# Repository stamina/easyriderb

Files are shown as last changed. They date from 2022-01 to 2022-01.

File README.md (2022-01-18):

EasyRider
=========

This project is frozen. It's here for archival/educational purposes.

_UPDATE:_ EasyRider REV C is a completely new project, it is based on
a way more powerful (32bit instead of 8bit) STM32 Arm Cortex M4 microcontroller.

EasyRider REV B is a motorcycle telemetrics project, developed specifically for my Honda C90 classic bike.
It uses more advanced code and SMD components than Rev A.

The software is written in bare-metal C for the Atmel AVR ATmega1284p 8bit microcontroller.

The PCB was created with Altium, you'll find the gerbers/schematics/datasheets in the /docs directory.

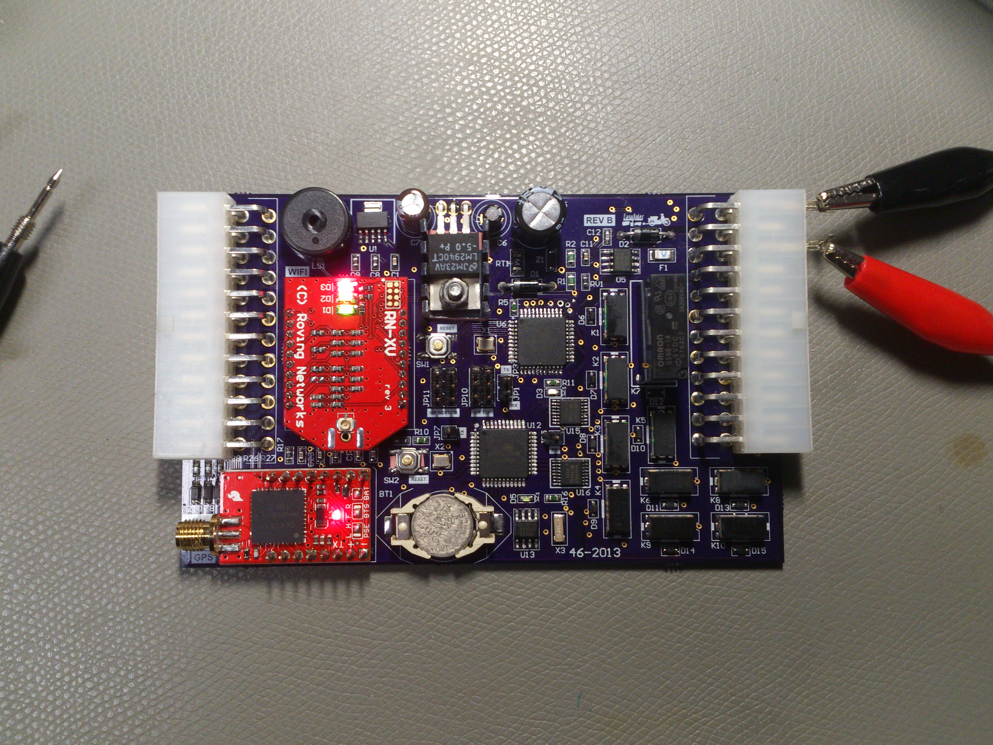
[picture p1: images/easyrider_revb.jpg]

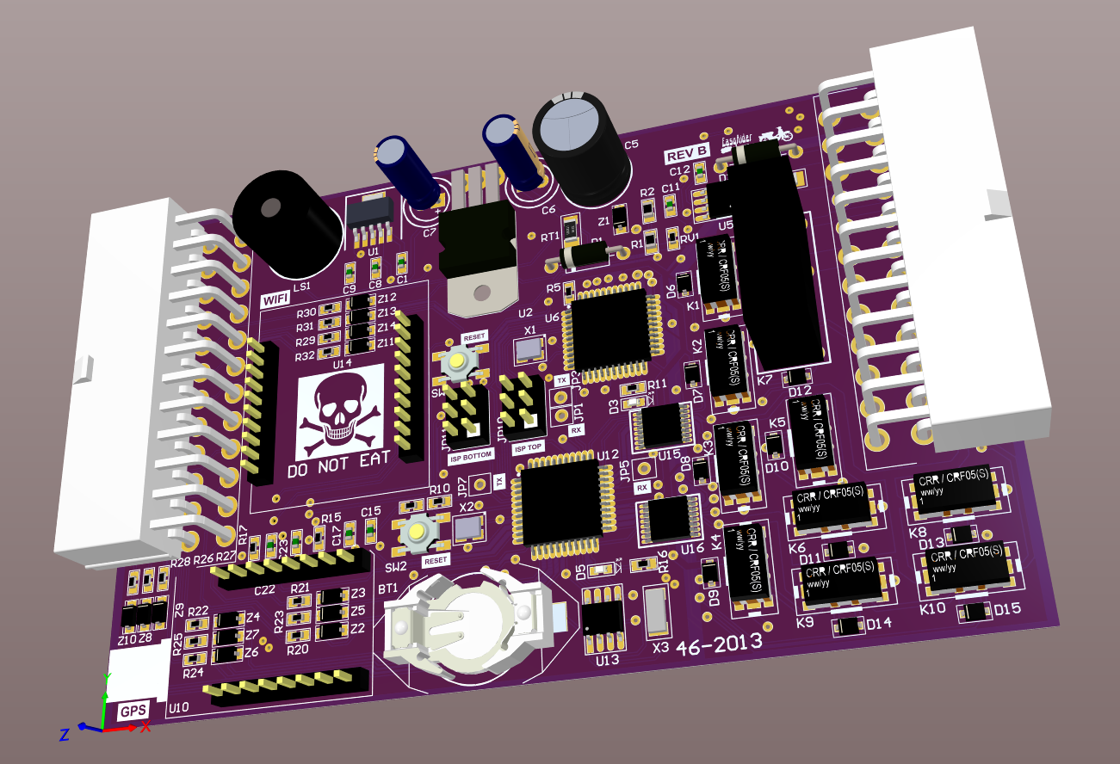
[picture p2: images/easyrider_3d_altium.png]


Functionality
-------------

EasyRider basically does the following things:

- Controls the lighting system: indicators, rear light, brake light, etc.
- Controls the claxon
- Contains a simple alarm system, based on an accelerometer
- Reads the motorcycle battery voltage and the power draw of the board
- Contains a little buzzer for some startup/alarm sounds
- Reads the RPM of the motor via the CDI, through an opamp and optocoupled circuit
- Logs GPS coordinates and timestamps of events via the external RTC
- Sends all telemetry data over Wifi or writes it to the microSD card

Notable components
------------------
2x Atmel AVR ATmega1284P microcontrollers
1x Accelerometer MMA7361L board
1x GPS Venus638FLPx sparkfun board
1x WiFly-RN-XV-DS sparkfun board
1x lm35 temperature sensor
9x Meder reed relays CRR05-1A
1x Opamp tlv2371
1x Optocoupler vo610a
1x Real Time Clock DS1307.pdf
2x uln2003lv transistor arrays

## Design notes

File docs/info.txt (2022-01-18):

*info.txt* easyrider rev B
" vim: filetype=help foldmethod=marker foldmarker=<<<,>>> modifiable noreadonly tw=0
" Author: Bas Brugman
" Website: www.visionnaire.nl

EasyRider REV B
---------------

General functionality
---------------------

Steps for firmware setup new boards:

  1. Set correct fuses via avr.txt
  2. remove HALT bit from RTC register: run ds1307_start_osc() once from init
  3. setup GPS (default baudrate is 9600 -> setting to 56700):
     3 uart strings with baud rate, 10hz and binary msg only
     -> Paste them from setup.h into mcu2 .c file
  4. setup WIFI via UART commands:
     Default baudrate is 9600, change this after initial setup to 57600
     Firmware update to 4.41, see below
     -> Serial setup of Wifly is done by the cutecom or moserial terminal program.
     -> Paste the pass-through UART code from setup.h into mcu1 .c file

Communication
-------------

[X] SPI bus (for MCU intercommunication and microSD card reading/writing):

  System Commands API (SPI Intercommunication between mcu's to exchange data)

  SPI Intercommunication conditions and command logic:

  SPI speed: fosc/4 (20 Mhz) -> 5 Mhz

  MCU intercommunication time per byte is: 32 (8 bits*4 prescaler) cycles + 2 gap cycles + 5us delay added per byte ->

  6.7us per byte -> 145 Kbyte/sec throughput

  Per second througput needed:

  mcu1 IN buffer:
    10x ~96 bytes GPS
    10x ~44 bytes DATA
        ~49 bytes other triggered cmds

  mcu2 IN buffer:
    10x ~29 bytes STATS
       ~119 bytes other triggered cmds

  Feedback / Flow Control / Queueing system:

  OnChange triggered commands have higher priority than Timed command triggers, so they stop/flush the current out cmds buffers and take
  over the communication buffers.

  SPI Flow between both mcu's and WiFi module:

app     <--------[ wifi or serial (uart0/1 from mcu1 ]---------->    mcu1      <----------[ SPI ]------------->    mcu2
=======================================================================================================================
                                                                            state change trigger <---  CMD_STATE  ('a')
                                <--- mcu1 response <--- CMD_STATE ('a')
  ---------------------------------------------------------------------------------------------------------------------
                                                                        periodic trigger <---  CMD_STATS ('b') (10 t/s)
                                                          mcu 1 response ---> CMD_STATS ('b')
  ---------------------------------------------------------------------------------------------------------------------
                                                                         periodic trigger <---  CMD_DATA ('c') (10 t/s)
                                <--- mcu1 response  <--- CMD_DATA ('c')
  ---------------------------------------------------------------------------------------------------------------------
                                                                          periodic trigger <---  CMD_GPS ('d') (10 t/s)
                                 <--- mcu1 response  <--- CMD_GPS ('d')
  ---------------------------------------------------------------------------------------------------------------------
                  --->   on app trigger ---> CMD_RTC ('e')
                                                           CMD_RTC ('e') ---> on response ---> 
  ---------------------------------------------------------------------------------------------------------------------
                  --->   on app trigger ---> CMD_SENSE ('f')
                                                           CMD_SENSE ('f') --> on response ---> 
  ---------------------------------------------------------------------------------------------------------------------
                  --->   on app trigger ---> CMD_SETTINGS ('g')
                                                           CMD_SETTINGS ('g') --> on response ---> 
  ---------------------------------------------------------------------------------------------------------------------
                  --->   on app trigger ---> CMD_LOG ('h')
                                                           CMD_LOG ('h') --> on response ---> 
                                                                                     <----- on response  CMD_LOG ('h')
  ---------------------------------------------------------------------------------------------------------------------
                  --->   on app trigger ---> CMD_REBOOT ('i')
                                                           CMD_REBOOT ('i') --> on response ---> 
  ---------------------------------------------------------------------------------------------------------------------
                  --->   on app trigger ---> CMD_PINCODE ('j')
                                                           CMD_PINCODE ('j') --> on response ---> 
  ---------------------------------------------------------------------------------------------------------------------
                                                                                         trigger <---  CMD_SOUND ('k')
                  --->   on app trigger ---> CMD_SOUND ('k')
                                                          mcu 1 handler ('k')
  ---------------------------------------------------------------------------------------------------------------------
                                                                                            trigger <---  CMD_MSG ('l')
                                                           response ('l')
  ---------------------------------------------------------------------------------------------------------------------

  [X] MCU2 is master, MCU1 is slave
    [X] FIX: SS on mcu2 is a input GPIO: SI_LI (left indicator psense) -> ignore EV_LI_ON/EV_LI_OFF during each SPI transfer,
        since SS must be temporarily set as an output(low), then output(high) to not interfere with the hardware SPI
  [X] SPI communication queuing algorithm
      SPI tips: -> http://rpc.gehennom.org/2013/09/atmega2560-as-an-spi-slave/
  [X] SPI commands' payload bytes always have to be in ascii format
  [ ] Command info: 

      Package: CMD_START - CMD_CODE - PAYLOAD BYTES (ASCII) - CMD_STOP

      All OUTGOING commands contain a fixed timestamp: [Dddmmyyhhmmssmmm] prepended to the payload data

      [X] command name:               CMD_STATE
          command code:               'a'
          payload:                    [Dddmmyyhhmmssmmm] + high_state_byte + low_state_byte as ascii string: 00000000.00000000
          period:                     state change trigger
          info:                       notify mcu1 of every state change and transfer the full new state
          direction:                  mcu2 -> mcu1 -> app
          examples:                   Dddmmyyhhmmssmmm00000000.00001010

      [X] command name:               CMD_STATS
          command code:               'b'
          payload:                    none for mcu2 polling, 28 stats ascii bytes for mcu1 as return
                                      [xxxyyyzzzCCCCVVVVVTTTTRRRRRG]
                                      xyz accelerometer, current, voltage, temperature, rpm and gear
          period:                     10 times/sec
          info:                       general polling for mcu1 commands (gear and statistics), since mcu2 is the master who can only initiate the communication 
          direction:                  mcu2 -> mcu1 / mcu1 -> mcu2
          examples:                   3403701080250119954214000001

      [X] command name:               CMD_DATA
          command code:               'c'
          payload:                    [Dddmmyyhhmmssmmm] + 28 stats ascii byte of sxyz accel/current/voltage/temp/rpm/gear data
          period:                     10 times/sec
          info:                       sending all sensor data values
          direction:                  mcu2 -> mcu1 -> app
          examples:                   Dddmmyyhhmmssmmm3403701080250119954214000001

      [ ] command name: gps
          command code: 'd'
          payload:       comma separated variable-length string of GPS information
          period:       periodically triggered by mcu2, 10 times/sec interval (10hz GPS module output)
          info:         sending of GPS data
          direction:    mcu2 -> mcu1 -> app

      [ ] command name: rtc
          command code: 0x85
          payload:      new timestamp 16 bytes
          period:       triggered by app
          info:         set the new current date/time for the RTC chip
          direction:    mcu1 -> mcu2

      [ ] command name: CMD_SENSE
          command code: 0x86
          payload:      3 bytes representing the 16bit d_sense_status/p_sense_status/d_sense_active values
          period:       triggered by app
          info:         These 3 bytes basically change the values at runtime. Default values are set in the EEPROM.
                        d_sense_status and p_sense_status are exclusive, one or the other has to be toggled OFF (0x00). 
          direction:    app -> mcu1 -> mcu2

      [ ] command name: CMD_SETTINGS
          command code: 'g'
          payload:      empty params to fetch current EEPROM values | data to fill new EEPROM | pincode or supervisor pincode to reset to default
          period:       triggered by app
          info:         sending 8 data values
          direction:    app -> mcu1 -> mcu2 / app <- mcu1 <- mcu2

      [ ] command name: log
          command code: 0x88
          payload:       log day: ddMMYYYY
          period:       triggered by app
          info:         requests log records from the SD card from a certain day
          direction:    app -> mcu1 -> mcu2 / app <- mcu1 <- mcu2

      [ ] command name: reboot
          command code: 0x89
          payload:       none
          period:       triggered by app
          info:         Reboot command send to both mcu1/mcu2, lets the watchdog timer run out and reboot both chips
          direction:    app -> mcu1 -> mcu2

      [ ] command name: pincode
          command code: 0x90
          payload:       4 numbers
          period:       triggered by app
          info:         authentication of app, without the pincode nothing (no commands allowed) is sent over Wifi
          direction:    app -> mcu1 -> mcu2

      [X] command name:               CMD_SOUND
          command code:               'k'
          payload:                    1 byte [0-255] 0-252: index of song, 255: randomly picked sound,
                                      254: no sound (SOUND_OFF), 253: monotone beep (SOUND_ON)
          period:                     triggered by app
          info:                       plays a little song or beep
          direction:                  mcu2 -> mcu1 / app -> mcu1
          examples:                   255

      [ ] command name: CMD_MSG
          command code: 'l'
          payload:       0
          period:       triggered by app
          info:         General notifications sent from mcu1/mcu2, 3 levels: NOTICE/WARNING/ERROR
          direction:    app -> mcu1 -> mcu2 / .....
          examples:

      [ ] command name: CMD_TEST
          command code: 'm'
          payload:       0
          period:       triggered by app or sense
          info:         POST (Power On Self Test)      
                        Procedure to test EEPROM, etc.....
          direction:    app -> mcu1 -> mcu2 / .....
          examples:

---------------------------------------------------------------------------------------------------------------------
TODO's/BUGS before releasing firmware 1.0.0
  [X] timestamp update niet -> check mcu2 update code
  [X] ACTIVE/SLEEP states keep toggling when activating IGN_SENSE, cause:
      -> physical senses fire an ON event and dynamic senses immediately fire an OFF event
      fix: set d_senses_active 0 by default and disable p_senses_active when toggling on d_senses_active and vice versa.
      Toggling these senses is the responsibility of the "blackadder" app.
  [X] CMD_STATE is not getting through to mcu1?!
      cause: BUSY flag flushes the out_payloads by consecutive calls, before its being send
      fix: remove reset_out(), not needed since the data in the out_buffer is send fast enough to overload
  [X] after settle, some lights are not getting on again
      cause: states are set first, then when the settle runs out, it turns all lights off again with all_relays()
      fix: remove SETTLE functionality, since its obsolete, self-check is an APP feature
  [X] MCU2 stats_handler -> should save stats, like g_gear for neutral light check and accelerometer values for alarm
  [X] BUG: buzzer doesnt produce sounds, found a conflict with RPM pin T0 external timer
      PB3 of buzzer has the OC0A functionality turned on, which overwrites are frequencies pushed on that pin
      fix: disable OC0A on the PB3 pin
  [ ] no GPS binary chars, after fix -> debug venus.c 
  [ ] braking hard (read accelerometer) -> hazard light mode on (brake+flashing knipperbollen)
    -> EXPERIMENT byte opnemen in Settings rom -> 8 bits als flag hiervoor gebruiken
  [ ] Add extra song (convert ruby script to python, use MIDICSV) -> HOTRS/The Animals.
    -> midi2byte.rb and midi2byte.py
    -> http://www.fourmilab.ch/webtools/midicsv/ 
---------------------------------------------------------------------------------------------------------------------
[X] Test "stats", measure all ADC conversions and make possible corrections
[X] Extra util.c/.h toevoegen, voor global converter functies zoals "byte to binary ascii", "0-left-padding", ...
[X] General Settings in EEPROM:
    -> Default settings in FLASH
    -> data validation when doing EEPROM reads/writes -> checking for valid "easyrider" string
[ ] Physical Senses/Dynamic Senses functionality
    [ ] enable/disable functionality for:
      -> g_p_senses_active (firmware flags to allow/disallow senses)
      -> g_d_senses_active (client app flags to allow/disallow senses)
      -> g_d_senses_status (client app flags to (de-)activate senses)
[X] Migrate websocket.c/h to raw byte streams -> wifi.c/h
[ ] UART1 commandline terminal prompt (on MCU1 only)
   [ ] rewrite command_usart.c/h -> terminal.c/h
   [ ] ability to launch all commands as a "fallback mode" in case Wifi communication fails
   [ ] small help menu containing all commands and some examples
      -> menu accessible with ?, help and ENTER key
[X] Sound system (Speaker beeps):
      mcu2 triggers and sends the CMD_SOUND to mcu1
      mcu1 plays or mutes the sound over the speaker
      e.g. in ST_SLEEP mode, all sounds will be muted, IGN_ON event fires a startup sound.
      Settings.startup_sound defaults:
      255: randomly picked sound
      254: no sound (SOUND_OFF)
      253: monotone beep (SOUND_ON)
      [0-252] index of music array to play song
[ ] MicroSD card FatFS library implementation (see thread: http://www.avrfreaks.net/forum/tut-c-getting-sdmmc-card-working-painlessly-fatfs?page=all)
  [ ] Logging to microSD card, FAT32 code library -> SDHC card compatibility
    -> Log filenames follow the format: ddmmyyyy.[bootup number] -> example "23122015.001"
    -> After succesful transfer, delete file (don't exceed file limit in root dir of SD card)
    -> log every command, in timestamp + data format
  [ ] All possible logfile rows with example data:
      CMD_STATE       'a' 
      CMD_STATS       'b' 
      CMD_DATA        'c' 
      CMD_GPS         'd' 
      CMD_RTC         'e' 
      CMD_SENSE       'f' 
      CMD_SETTINGS    'g' 
      CMD_LOG         'h' 
      CMD_REBOOT      'i' 
      CMD_PINCODE     'j' 
      CMD_SOUND       'k' 
      CMD_MSG         'l' 
[ ] Change alarm algorithm:
    1. Alarm SENSE (toggle switch) keeps triggering ALARM_OFF/ON events
    [ ] Ignition toggle will set the actual ALARM on/off mode
    [ ] Alarm accelerometer values are saved after x secs and the alarm will be ready to be triggered
[X] Check all states/transitions and do some cleanup
  [X] removing unnecessary states like ST_ALARM_SET/ST_SETTLE/ST_CONNECTED/ST_LOG
  [X] rename ST_IDLE to ST_ACTIVE
  [X] create state-transition diagram
  [X] All possible states/substates :
    ST_SLEEP (Mutally Exclusive with ST_ALARM/ST_ACTIVE, main state)
    ST_ACTIVE (Mutally Exclusive with ST_ALARM/ST_SLEEP, main state)        
    ST_ALARM (Mutally Exclusive with ST_ACTIVE/ST_SLEEP, main state)        
    ST_ALARM_SET
    ST_NEUTRAL
    ST_RI (Mutually Exclusive with ST_LI)
    ST_LI (Mutually Exclusive with ST_RI)
    ST_CLAXON
    ST_BRAKE
    ST_LIGHT
    ST_WARNING
    ST_PILOT
[X] ST_NEUTRAL instead of ST_DEEP_SLEEP -> status light ON/OFF
[X] Debug info/traces over UART1's
[X] Timestamp format and functionality: [Dddmmyyhhmmssmmm] (D stands for day number: 1-7)
    2 separate clocks used: RTC + internal MCU millisecond timer -> 25hz RTC polling, millisecond timer is reset per RTC Second change.
[X] Uitlezen RTC via I2C (revB hardware limitation: no sync pulse connected to reset ms timer, evertime a second rolls over):
    -> event occurred -> read RTC, seconds accuracy -> add separate ms timer (3 digits) -> dd-mm-yyyy hh:mm:ss mmm
[X] Current-sensor: ACS714ELCTR-05B-T 5V/5A -> zie https://www.sparkfun.com/products/8883 voor opamp gain en tips
    -> Readout info: 3 part series: https://www.youtube.com/watch?v=UF5jrnXvTlM
[X] External changes :
    [X] Ophanging/Scheiding draadboom -> niet te dicht bij bobine
    [X] Snubber voor claxon op aparte
      -> 1x flyback diode (snubber) parallel across claxon: SB540E SCHOTTKY 40V 5A
    [X] 1x 10 ohm 5 watt resistor for rear light dimming
    [X] 3D Case/Behuizing ontwerpen in Blender voor 3D printing shapeways.com:
      PCB binnenmaten/boardmaat zonder marge: 75.16mm x 120.17mm x 20mm(van top tot bottom highest component) (wxlxh)
      buitenmaten restricties:  26mm-27mm maximale hoogte
      -> Export .step file from Altium -> convert to .x3d file with http://www.cadexchanger.com -> import into Blender 
    [X] mini-fan integreren in behuizing -> Sunon mini-fan Sunon 20 mm - 5 V Fan - Brand New - Low S/H - KDE0501 KDE0501PDB3-8
[X] Molex 24pin angled connector
    -> Vin/GND als eerste 
[X] Battery backup for RTC -> cr1225
[X] Headers for wifi/gps breakouts
[X] USART TXB0104 levelshifter tussen AVR en SD card -> SPI
[X] Logo's voor breakouts -> AVRISP, WIFI, GPS en ACCEL. (Ook x/y/z arrow vermelden)
[X] RPM meten vanaf pulse van hall sensor op vliegwiel:
    -> rectifier diode + voltage divider + opamp buffer + optocoupler
    -> falling edge counter, welke pin? INT0?
    -> Engine RPM counter: http://www.avrfreaks.net/index.php?name=PNphpBB2&file=printview&t=43519&start=0
    [X] BUG: rpm value reset niet naar 0, wanneer de motor uitgaat
[X] Vergroten range van accu ADC -> 10v tot 15v -> naar 10bit ADC -> 1/3 voltage divider: 2.2k/1k
[X] Wifly module setup
    LED information ->
      D1: green slow blink (module active)
      D2: orange fast blinking (data send out)
      D3: 
    -> Config example: http://www.curiousmarc.com/dome-automation/building-marcduino-boards/setting-up-the-wifly-radio
    [X] Update firmware from 2.32 to 4.41 via these UART commands:
      $$$                                               [re-enter command mode, NOTE: send no <CR> for this one only]
      set wlan join 1                                   [join WiFi from ssid and passphrase]
      set wlan ssid    Your-Home-Wifi-SSID-Here         [your home Wifi networkname]
      set wlan phrase Your-Home-Wifi-Password-Here      [you password, probably WPA2 security]
      set ip dhcp 1                                     [get ip address from dhcp server]
      set ftp address 198.175.253.161                   [new ftp address of the update server ftp://rn.microchip.com/public/]
      set ftp dir public                                [download dir, default should be OK]
      set ftp user roving                               [ftp user name, default should be OK]
      set ftp pass Pass123                              [ftp password, default should be OK]
      save
      reboot
      $$$
      ftp update wifly7-441.img                         [specifically downloads 4.41]
      reboot
      $$$
      factory R                                         [so it does not complain about a "CFG-ERR" or bad config]
      save
      reboot
    [X] Wifly SoftAP mode setup via these UART commands:
      set wlan join 7                    [enables Access Point mode -> soft AP mode]
      set ip dhcp 4                      [enables DHCP server]
      set ip address 192.168.2.1         [or choose any other IP address]
      set ip gateway 192.168.2.1         [for Mobile Phone/Laptop to connect to, gateway needs to be the same as the IP address]
      set ip netmask 255.255.255.0       [netmask ip]
      set apmode ssid easyrider#         [or any other name you choose for you R2 Wifi network]
      set apmode pass password           [set your WiFi password/passphrase(WPA2–PSK) here, needs to be at least 8 characters long, max 32]
      set wlan rate 0                    [throttle down speed for longest reach 0=1Mbit/sec, default is 12=24Mbit/sec]
      set wlan channel 3                 [or any 2.4GHz channel number you like, I think there are 7]
      set apmode link_monitor 0          [disables auto deauthentication of clients, default is 3600]
      save
      reboot 
    [X] Extra commands:
      set uart baud 57600                [change baudrate of tx/rx pins]
      set comm remote 0                  [don't send a default TCP '*HELLO*' when opening a tcp connection]
      set comm open 0                    [don't send a default UART '*OPEN*' when opening a tcp connection]
      set comm close 0                   [don't send a default UART '*CLOSE*' when closing a tcp connection]
      get wlan                           [show wlan settings]
      get everything                     [show all settings]
Wifi Wifly info:
  Soft AP Mode -> "The module runs a DHCP server and issues IP addresses to seven clients"

  Normal mode msg should be something like this:
  **********************************************
          *READY*

          Using WPA2-PSK
          AP mode as easyrider2 on chan 3
          Listen on 2000

          DHCP Server Init
  **********************************************

  Command mode is entered with $$$, no CR or LF! Commands need a CR though.

[X] UART communication:
          AVR <-> FTDI cable <-> Terminal (Serial Terminal 57600 8N1)
          AVR <-> WIFI module <-> Terminal (Telnet to port 2000, tcp/ip)
[X] "websocket" text frames pushed via UART0 to Wifly's TCP/IP stack
  Websockets information and examples:
    -> RFC: http://tools.ietf.org/html/rfc6455
    -> Some good general explanation: http://lucumr.pocoo.org/2012/9/24/websockets-101/
    -> http://jlectronique.org/WebsocketsEN.htm
    -> https://github.com/ejeklint/ArduinoWebsocketServer
    e> https://github.com/m8rge/cwebsocket
    [X] Websocket frames: Payload data altijd tussen 0-125 bytes houden
[X] GPS coordinates
     -> GPS Venus module via mcu2 UART0
     -> configure via binary command set to send uart_put commands (decimals) in a row (save to gps' internal flash):
[X] BUG: Minor tweak to CTC timer values to correspond to the correct formula: CTC # = (required delay in sec)/(clock time period in sec)-1 
[X] BUG: Claxon mosfet switched aan bij veel toeren, voor zeer korte tijd -> oscillation?
      -> FIXED: Gemeten met scope: elke keer precies 15ms gate trigger, dus physical sense (drukknop claxon) maakt
         contact -> vergroten van 3x 5ms "debouncing" algoritme in code naar 6x NOTE: this was the final fix!
      -> duikt de 12V op gate naar beneden? waarom?
      -> Cap ervoor zetten?
      -> Grotere input cap bij 12V Regulator -> 1000uf, niet te hoge dimensie
      -> Transistor base resistor van 10K naar 2200 ohm?
      -> Cooler verwijderen: te veel capacitance?
      -> extra flyback diode (schottky) parallel aan mosfet? 
[X] BUG: The claxon sound continues when turning the alarm off by turning the ignition key on 
[X] TODO: Alarm mode: indicator blink slower -> every 4 timer1 ticks: 1 tick on 
[X] TODO: Alarm trigger time should be faster, 
[X] BUG: Ignition off: disable all lights/sounds
[X] BUG: Cockpit status light stays lit in alarm/alarmsettle mode ->  unwanted check_battery_read() calls
[X] BUG: Hardware related:  when claxon (2 amp) is pushed, all reed relays switch on: short blinks of lights
      -> snubber/flyback diode proberen
      -> Ground path van claxon terugvoeren via draad naar accu min-pole om groundloops te voorkomen
[X] BUG: Alarm trigger werkt niet lekker: claxon/blinkers sequence niet goed en transition from alarm_settle/alarm states foutief
- [X] Lighting System
- [X] Audio through Claxon and Buzzer
- [X] Battery status
- [X] Alarm, triggered by an accelerometer

- General functionality:
  [X] State Machine rules "exclusive"/"inclusive"
      [X] positive and negative substates parsing
      [X] sense reading moet uit te zetten zijn: enableSense/disableSense
      [X] event dispatching via psense reads, maar ook via dynamic senses (dyn_senses)
  [X] JTD uitzetten, zodat de poorten normaal gebruikt kunnen worden ->
       An IO control bit "JTD" is available. Unlike the fuses this bit can be
       set at run-time allowing you to disable the JTAG / OCD functionality in software
       during program execution.
  [X] Watchdog aanzetten, tegen vastlopers!
  [X] In production: OCD uitzetten ivm extra stroomverbruik

- Audio
  [X] Simple music via buzzer (Midi to CSV to .h binary conversion)

 [X] Claxon
  [X] Sound on Push button

 - Battery status
    [X] knipper status light cockpit:
      [X] normal operation -> continue branden
      [X] shutdown via switch -> uit
      [X] indien low battery -> slow knipper
      [X] indien high battery -> fast knipper

 - Alarm, triggered by an accelerometer
    [X] bij aanzetten -> 1x indicators aan voor x secs -> alarm settle time -> buzzer music
    [X] in active mode: cockpit indicator lamp knippert
    [X] Alarm triggered: alle lichten blinken, claxon repeat
    [X] Alarm triggered: na x secs -> reset -> accelerometer slaat nieuwe voltage waarden op

 - Light/Buzzer System
    [X] Indicators Left/Right
      [X] Buzzer mee laten piepen (software flag)
    [X] Rearlight
    [X] Brakelight
    [X] Pilotlight
    [X] Warning lights: 4x knipperbollen blinken en buzzer

- Contact slot:
  Ignition uit: sense wire (SENSE_IGN) -> contact uit
    [X] naar ST_SLEEP mode
    [X] Na x secs naar mcu hardware sleep mode
      -> uitzetten van ADC, Watchdog en ports
      -> geen wakeup trigger, alleen een harde reset
  Ignition aan: sense wire (~SENSE_IGN) -> contact aan:
    [X] Alle lampen een paar seconden aan
    [X] startup sound / kleine muziekje
    [X] status wordt ST_NORMAL

- Shell Commands:
    [X] help -> show help menu / service menu
    [X] show
        [X] version
        [X] state (all substates / physical and dynamic senses)
        [X] volt (accu voltage / 3-axis voltages accelerometer)
        [X] conf (EEPROM struct, toon alle tSettings tegelijk):
    [X] set 
        [X] dynamic senses
        [X] conf (settings in EEPROM struct)
    [X] reset (software reset mcu via watchdog)

GPS module
----------

Aansturing gaat via UART0 van mcu2, zie pdf voor alle commando's.
Gebruikmakend van de binary output message. Disabled all NMEA string messages.

Functies van https://code.google.com/p/multiwii/source/browse/branches/guru_florida/2.4/MultiWii_shared/Venus.cpp?r=1767
bekijken en implementeren in seperate lib venus.c/venus.h

Huidige firmware response:

$SkyTraq,Venus6
$Kernel,v1.6.10,00030ED
E,16324205,F,16.367667MHz
$ver,011023,rev,120710

Configuration C-code:

// 57600 baud
uart_put_0(160);
uart_put_0(161);
uart_put_0(0x00);
uart_put_0(0x04);
uart_put_0(0x05);
uart_put_0(0x00);
uart_put_0(0x04);
uart_put_0(0x01);
uart_put_0(0x00);
uart_put_0(13);
uart_put_0(10);

// Binary only output
uart_put_0(160);
uart_put_0(161);
uart_put_0(0x00);
uart_put_0(0x03);
uart_put_0(0x09);
uart_put_0(0x02);
uart_put_0(0x01);
uart_put_0(10);
uart_put_0(13);
uart_put_0(10);

// 10 hz update rate
uart_put_0(160);
uart_put_0(161);      
uart_put_0(0x00);
uart_put_0(0x03);
uart_put_0(14);
uart_put_0(10);
uart_put_0(0x01);
uart_put_0(0x05);
uart_put_0(13);
uart_put_0(10);

Some forum excerpt:

"you need to supply the battery pin (with the same wire than 3.3V power supply, or with a battery !).
To modify parameters, find attached a file I have built to summarise the different commands (in french, but easy to understand), and messages specif in pdf file.
You will just have to send these data (provided in my file in decimal format).

Be careful:
- if you change values, you will have to change the checksum (Excusive OR of all data bytes (complete PAYLOAD))
- if you change parameters in RAM, they will be resetted at the next turn on. But they will remain if you set them in flash.
"

Initialisation du port 3 à 9600 Bd

======================================================== 

Débit du port en RAM:
4800	: 160 161 00 04 05 00 00 00 05 13 10
9600	: 160 161 00 04 05 00 01 00 04 13 10	
19200	: 160 161 00 04 05 00 02 00 07 13 10
38400	: 160 161 00 04 05 00 03 00 06 13 10
57600	: 160 161 00 04 05 00 04 00 01 13 10
115200	: 160 161 00 04 05 00 05 00 00 13 10

Débit du port en flash:
4800	: 160 161 00 04 05 00 00 01 03 13 10
9600	: 160 161 00 04 05 00 01 01 05 13 10
19200	: 160 161 00 04 05 00 02 01 06 13 10
38400	: 160 161 00 04 05 00 03 01 07 13 10
57600	: 160 161 00 04 05 00 04 01 00 13 10
115200	: 160 161 00 04 05 00 05 01 01 13 10

========================================================

Fréquence en RAM:
 1Hz	: 160 161 00 03 14 01 00 15 13 10
 2Hz	: 160 161 00 03 14 02 00 12 13 10
 4Hz	: 160 161 00 03 14 04 00 10 13 10 
 5Hz	: 160 161 00 03 14 05 00 11 13 10
 8Hz	: 160 161 00 03 14 08 00 06 13 10
10Hz	: 160 161 00 03 14 10 00 04 13 10

Fréquence, en flash:
 1Hz	: 160 161 00 03 14 01 01 14 13 10
 2Hz	: 160 161 00 03 14 02 01 13 13 10
 4Hz	: 160 161 00 03 14 04 01 11 13 10 
 5Hz	: 160 161 00 03 14 05 01 10 13 10
 8Hz	: 160 161 00 03 14 08 01 07 13 10
10Hz	: 160 161 00 03 14 10 01 05 13 10    

========================================================

Activation du WAAS en RAM:
ON	: 160 161 00 03 55 01 00 54 13 10
OFF   	: 160 161 00 03 55 00 00 55 13 10

Activation du WAAS en Flash:
ON	: 160 161 00 03 55 01 01 55 13 10
OFF   	: 160 161 00 03 55 00 01 54 13 10

==========================================================

Restart:
Hot	: 160 161 00 15 01 01 00 00 00 00 00 00 00 00 00 00 00 00 00 00 13 10
Warm	: 160 161 00 15 01 02 00 00 00 00 00 00 00 00 00 00 00 00 00 03 13 10 
Cold	: 160 161 00 15 01 03 00 00 00 00 00 00 00 00 00 00 00 00 00 02 13 10
Factory	: 160 161 00 02 04 01 05 13 10

===========================================================

Type de messages de sortie, en RAM:
aucun	: 160 161 00 03 09 00 00 09 13 10
NMEA	: 160 161 00 03 09 01 00 08 13 10
Binary	: 160 161 00 03 09 02 00 11 13 10

Type de messages de sortie, en Flash:
aucun	: 160 161 00 03 09 00 01 08 13 10
NMEA	: 160 161 00 03 09 01 01 09 13 10
Binary	: 160 161 00 03 09 02 01 10 13 10

Statistics
----------

Power Consumption
-----------------

(2.9Ah Gel battery)

Power EasyRider Board REV B:
  Normal mode:     xxx mA
  Sleep mode:      xxx mA (pcb led brandt nog!)
  Alarm mode:      xxx mA (indicator relay on/off)
  Deep Sleep mode: xxx mA (mcu Power Down) -> accu leeg na xx dagen

[X] PCB: purple solder mask and gold plating finish -> board house OSH Park in the US -> http://oshpark.com/

Altium Schematic/Board
----------------------

Used Altium version: 13.2.5 (2013)

General
-------

CTRL(-Shift)-TAB	Switch between open documents (tabs like schematic/pcb)

PCB Library
-----------

"Force Annotate", "Update from Libraries"

D-U		Update PCB with schematic changes
CTRL-M 		Measure distance between 2 points

Schematic 
---------

T, O		Search Library
V, D		View - Document Fit
V, F		View - Fit

PCB Editor
----------

"Update from PCB Libraries", "Rules" and finally "DRC" (Design Rule Checks)

Z, B		Zoom overview complete board
O, D	  View Configurations
O, L		Layer Configuration
(CTRL)-Q	Toggle metric/imperial
CTRL-G		Change current grid values
Shift-R		Change routing of track (ignore obstacles, around..)
V,B / 0, 9	Flip/Rotate board in 3D
N,S,A / N,S,O	Show ratnests all/selected
H,S,A / H,S,O	Hide ratnests all/selected 
Shift-S / + -	Toggle to single layer / walk through layers
CTRL-PrintScr	Screenshots
X and Y and L	Press while moving component to flip hor/ver and to other side of board

OSH Park Design Rules
---------------------

6 mil minimum trace width
6 mil minimum spacing
at least 15 mil clearances from traces to the edge of the board
13 mil minimum drill size
7 mil minimum annular ring

Logo's: 2de script optie van Altium wiki gebruiken, menu optie: DXP -> run script

Board cutouts/slots: they use a 0.1inch bit (so your minimum slot width is 0.1inch)

    boardname.GTL Top Layer
    boardname.GBL Bottom Layer
    boardname.GTS Top Soldermask
    boardname.GBS Bottom Soldermask
    boardname.GTO Top Silkscreen
    boardname.GBO Bottom Silkscreen
    boardname.GKO Board Outline
    boardname.G2L only if you're uploading a four layer board
    boardname.G3L only if you're uploading a four layer board
    boardname.XLN Drills

Keep out layer -> Design -> Board shape -> draw primitives on Keep Out layer, 6mil lines
File -> Fabrication Outputs -> Gerber files, select inch en 2:4, Advanced: absolute coordinates, keep zero's (belangrijk omdat de drill-file ook absolute is)
Check layers
Export -> Gerber, selecteer hier ook 2:4

Drills: 

Our service does not use Altium's Drill Drawing (DD1) or Drill Guide (GG1) files. We require that you produce the drill file in NC Drills format. 
Altium has published a guide on producing those files here:
http://wiki.altium.com/display/ADOH/NC+Drill+Output+Options

We require a 2:4 format when using Inches, or a 3:3 when using Millimeters.
Check "Keep Leading And Trailing Zeroes" and "Reference to absolute origin".
Uncheck "Generate Seperate NC Drill files", "Use Drilled Slot Command", and "Generate Board Edge Route Paths".
"Optimize Change Location Commands" doesn't matter, as we will recalculate drill movement.

Export -> Save Drill, hier ook 2:4, none en absolute selecteren

EOF

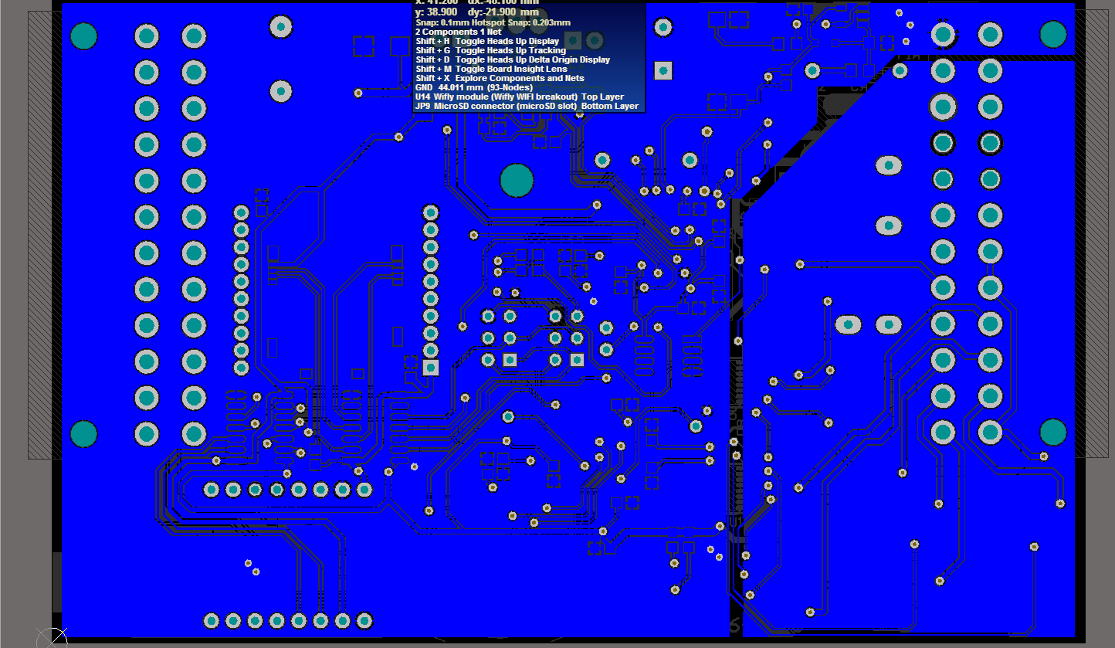
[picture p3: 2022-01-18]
images/easyriderb_bottomsignals.png

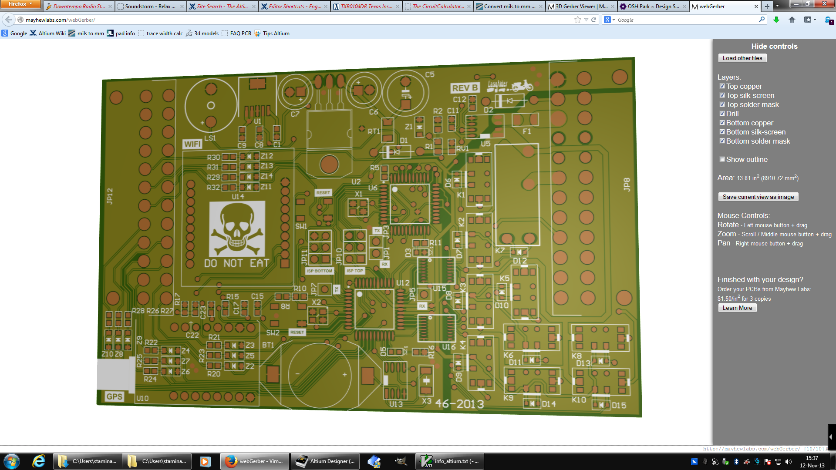
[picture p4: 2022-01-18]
images/easyriderb_onlinetop.png

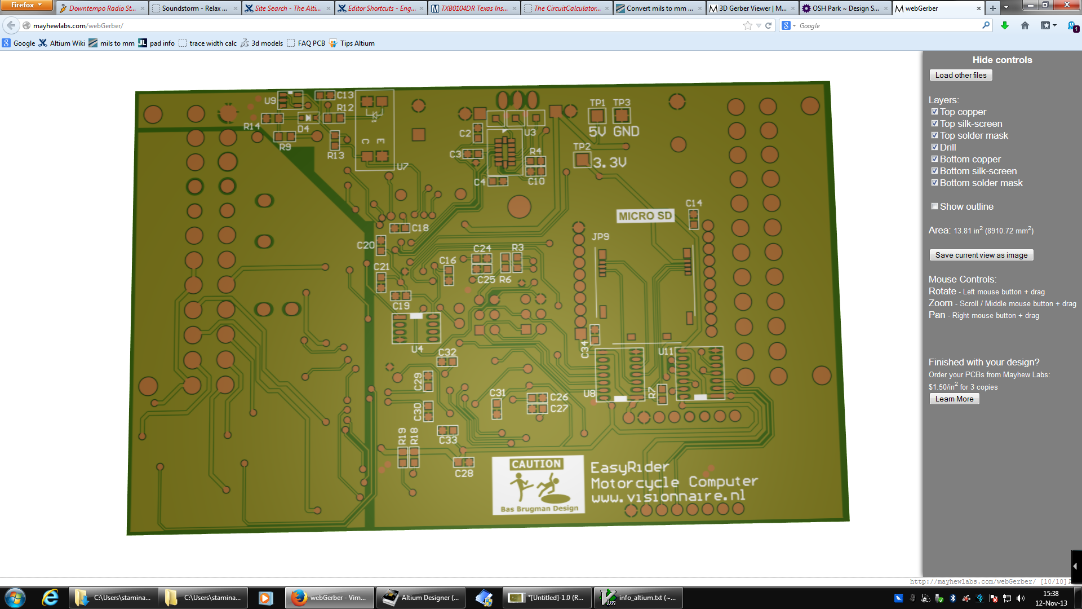
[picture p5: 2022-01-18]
images/easyriderb_onlinebottom.png

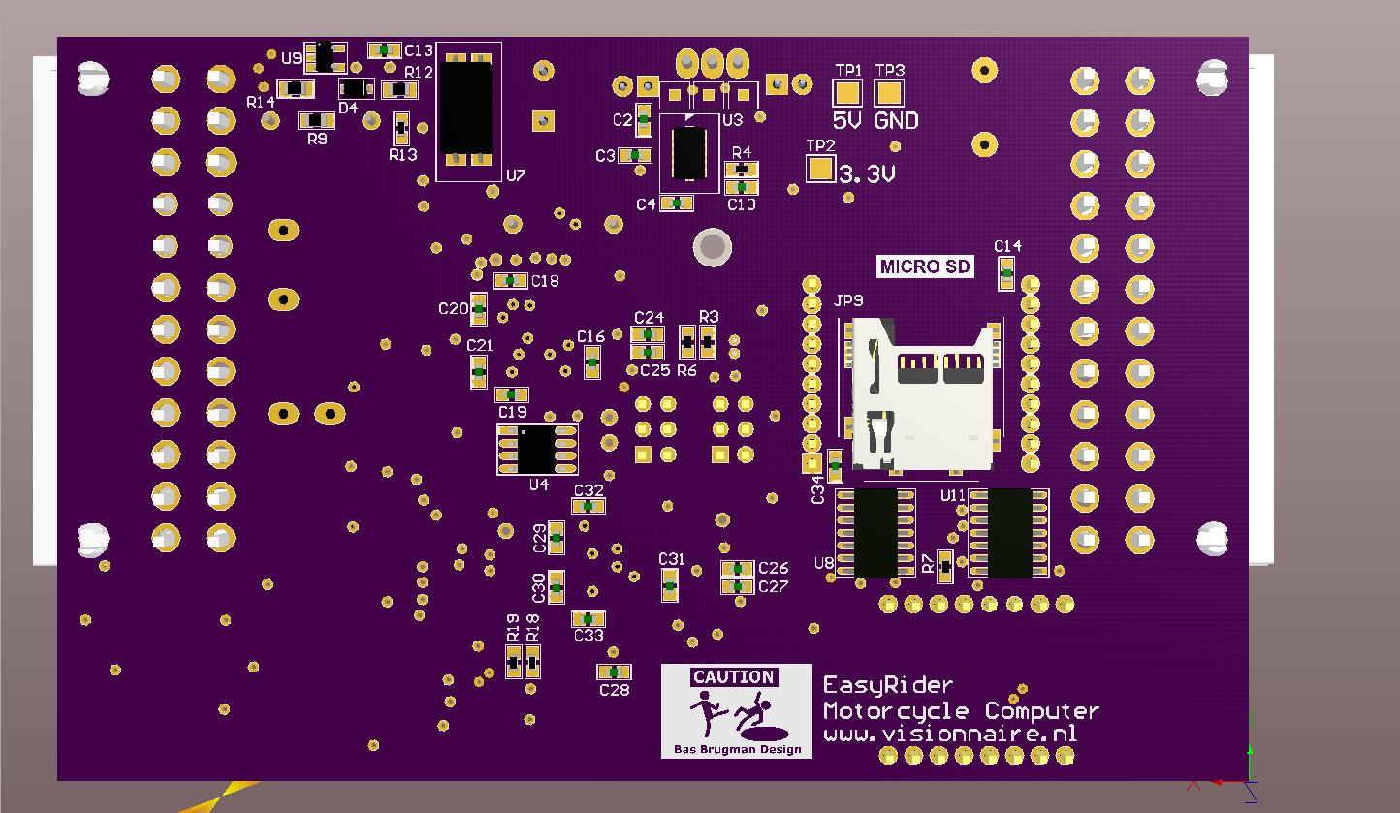
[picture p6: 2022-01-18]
images/easyriderb_back3d.png

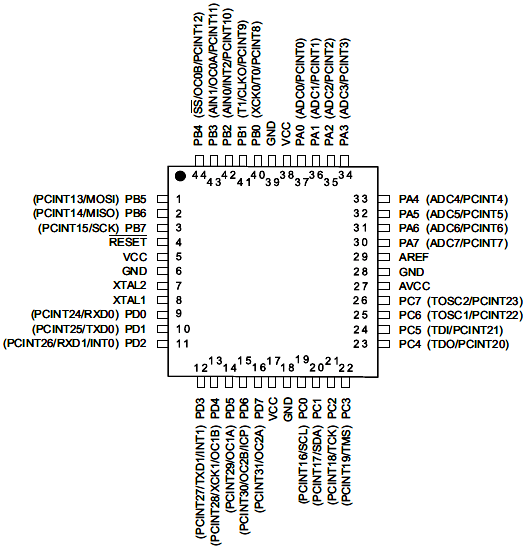
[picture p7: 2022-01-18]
images/ATMEGA1284P-AU_dim.png

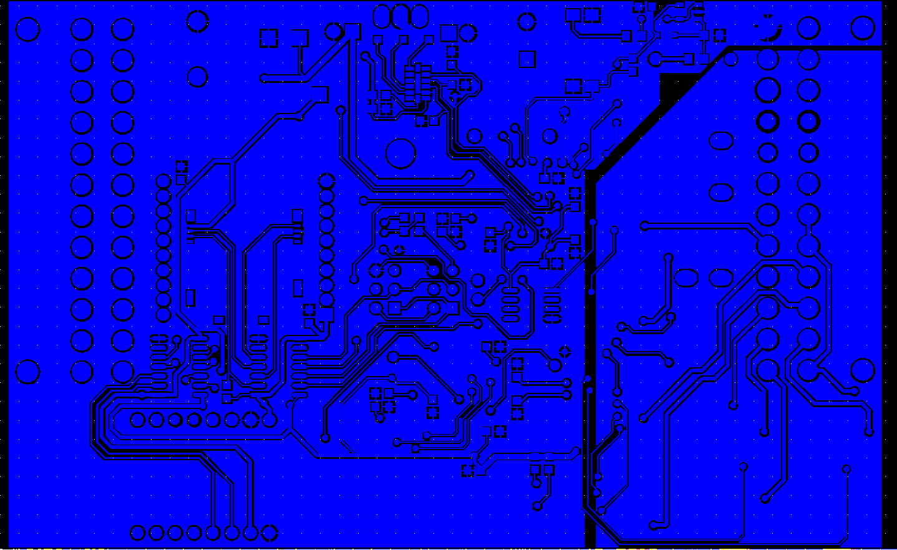
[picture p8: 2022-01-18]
images/easyriderb_bottomgerber_layer.png

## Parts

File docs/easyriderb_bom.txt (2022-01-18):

Quantity	Comment	Description	Designator	Footprint	LibRef

"1"	"CR1225 Battery"	"SMTU1225-LF"	"BT1"	"CR1225 Battery Holder"	"CR1225 Battery"
"1"	"0.01uF"	"CAPACITOR 0603"	"C1"	"0603C"	"0603C"
"3"	"3.3nF"	"CAPACITOR 0603"	"C2, C3, C4"	"0603C"	"0603C"
"1"	"470uF"	"CAPACITOR POLARISED Electrolytic TH"	"C5"	"CAP ELECTROLYTIC 5mm pitch"	"CAP-5MM"
"1"	"0.1uF"	"CAPACITOR POLARISED Electrolytic TH"	"C6"	"CAP ELECTROLYTIC 2.54mm pitch"	"CAP-2.54MM"
"1"	"47uF low ESR"	"CAPACITOR POLARISED Electrolytic TH"	"C7"	"CAP ELECTROLYTIC 2.54mm pitch"	"CAP-2.54MM"
"2"	"1uF"	"CAPACITOR 0603"	"C8, C9"	"0603C"	"0603C"
"20"	"0.1uF"	"CAPACITOR 0603"	"C10, C11, C13, C14, C15, C16, C17, C18, C19, C20, C21, C22, C23, C28, C29, C30, C31, C32, C33, C34"	"0603C"	"0603C"
"1"	"1nF"	"CAPACITOR 0603"	"C12"	"0603C"	"0603C"
"4"	"22pF"	"CAPACITOR 0603"	"C24, C25, C26, C27"	"0603C"	"0603C"
"2"	"1N4007"	"1N4001 DIODE"	"D1, D2"	"DIODE 1N400X"	"1N4001"
"2"	"LED"	"LED"	"D3, D5"	"LED 0603"	"LED 0603"
"11"	"1N4148"	"DIODE 1N4148 SOD323"	"D4, D6, D7, D8, D9, D10, D11, D12, D13, D14, D15"	"SOD323"	"DIODE 1N4148 SOD323"
"3"	"Comment"	""	"Designator1, Designator2, Designator3"	""	""
"1"	"Fuse 6A Slow Blow"	"SMD Fuse"	"F1"	"1206R/PTC"	"Fuse SMD 1206"
"4"	"uart debug"	"Test Point"	"JP1, JP3, JP5, JP7"	"Through Hole"	"Through Hole Pad"
"3"	"Pad"	"Test Point"	"JP2, JP4, JP6"	"Through Hole"	"Through Hole Pad"
"2"	"Mini-Fit Jr. Header 24pin angled"	"Mini-Fit® Jr. Header, Dual Row, Right Angle, with Snap-in Plastic Peg PCB Lock, 24 Circuits, PA Polyamide Nylon 6/6 94V-2"	"JP8, JP12"	"MOLEX 24PIN"	"Mini-Fit Jr. Header 24pin angled"
"1"	"MicroSD connector"	"SCHA5B0200 ALPS Memory Card Connectors microSD Rev Mount Push-push w/Switch"	"JP9"	"microSD slot"	"MicroSD connector"
"2"	"ISP HEADER"	"MCU In System Programming connector"	"JP10, JP11"	"HEADER-2X3"	"ISP HEADER"
"9"	"Meder Reed Relay"	"Reed Relays 1 Form A 5V SMT Low Profile"	"K1, K2, K3, K4, K5, K6, K8, K9, K10"	"MEDER Reed Relay CRR05-1A"	"Meder Reed Relay"
"1"	"3A Claxon Relay"	"General Purpose Relays Power PCB Relay 3A SPST-NO 5VDC"	"K7"	"RELAY"	"Relay-SPST"
"1"	"Buzzer"	"GENERIC PIEZO BUZZER"	"LS1"	"BUZZER PIEZO"	"PIEZO-GENERIC"
"1"	"2.2K"	"RESISTOR 0805"	"R1"	"0805R"	"0805R"
"1"	"1K"	"RESISTOR 0805"	"R2"	"0805R"	"0805R"
"6"	"10K"	"RESISTOR 0603"	"R3, R4, R8, R13, R18, R19"	"0603R"	"0603R"
"2"	"100K"	"RESISTOR 0603"	"R5, R7"	"0603R"	"0603R"
"15"	"330"	"RESISTOR 0603"	"R6, R10, R20, R21, R22, R23, R24, R25, R26, R27, R28, R29, R30, R31, R32"	"0603R"	"0603R"
"1"	"33K"	"RESISTOR 0805"	"R9"	"0805R"	"0805R"
"2"	"220"	"RESISTOR 0603"	"R11, R16"	"0603R"	"0603R"
"1"	"220"	"RESISTOR 0805"	"R12"	"0805R"	"0805R"
"1"	"6.8K"	"RESISTOR 0805"	"R14"	"0805R"	"0805R"
"2"	"50K"	"RESISTOR 0603"	"R15, R17"	"0603R"	"0603R"
"1"	"1A PTC"	"PTC"	"RT1"	"1206R/PTC"	"PTC 1206"
"1"	"18V"	"MOV 0603"	"RV1"	"0603R"	"MOV 0603 CT0603S14BG 18VDC"
"2"	"switch"	"PUSHBUTTON TACTILE SWITCH 5.2MM SMD"	"SW1, SW2"	"Tactile Button"	"SKQGADE010 ALPS SPST"
"3"	"Test Point"	"Test Point"	"TP1, TP2, TP3"	"Test Point"	"Test Point"
"1"	"3.3V Regulator"	"LDO Voltage Regulator High PSRR Fast RF High-Enable 500mA"	"U1"	"SOT223-6"	"VREG LDO 6pin"
"1"	"LM2940 5V Regulator"	"LINEAR REGULATOR"	"U2"	"to220h"	"VREG IGO"
"1"	"Accelerometer"	"Accelerometers 1.5G XYZ LOW G ANALOG"	"U3"	"MMA7361LCT"	"MMA7361LCT"
"1"	"LM35 temperature sensor"	"LM35 TEMPERATURE SENSOR"	"U4"	"SO8"	"LM35-SO8"
"1"	"Current Sensor"	"Hall Effect Current Sensor"	"U5"	"SO8"	"ACS714ELCTR-05B-T"
"2"	"ATmega1284P-AUR"	"8-bit AVR Microcontroller, 128KB Flash, 4KB EEPROM, 16KB SRAM, 44-pin TQFP, Industrial Grade (-40°C to 85°C), Reel"	"U6, U12"	"44A_M"	"ATmega1284P-AUR"
"1"	"Opto"	"Optocoupler SMD4"	"U7"	"Optocoupler SMD4"	"Optocoupler SMD4"
"1"	"TXB0104DR Level Shifter"	"Translation - Voltage Levels 4-Bit Bi-directional V-Level Translator"	"U8"	"SO14"	"TXB0104DR Level Shifter"
"1"	"TLV2371 opamp"	"OPAMP SOT23-5"	"U9"	"SOT23-5"	"TLV2371IDBVR"
"1"	"GPS Breakout Board"	"Venus GPS with SMA Connector"	"U10"	"GPS Breakout"	"GPS Breakout Board"
"1"	"TXS0104EDR Level Shifter"	"Translation - Voltage Levels 4B Bidirec Vltg- Level Translator"	"U11"	"SO14"	"TXS0104EDR Level Shifter"
"1"	"DS1307 Real Time Clock"	"Real Time Clock 64x8 Serial I2C RTC"	"U13"	"SO8"	"DS1307"
"1"	"Wifly module"	"Wifly RN-171 Wi-Fi module WiFly-RN-XV-DS"	"U14"	"Wifly WIFI breakout"	"Wifly module"
"2"	"ULN2003"	"Transistors Darlington Low Pwr 3.3V & 5V Relay Driver"	"U15, U16"	"TSSOP16"	"ULN2003"
"2"	"20 MHz"	"GENERIC CRYSTAL 4 Pins"	"X1, X2"	"XTAL"	"CRYSTAL 4P"
"1"	"32.768kHz"	"GENERIC CRYSTAL 2 Pins"	"X3"	"XTAL RTC"	"CRYSTAL 2P"
"14"	"5.6V"	"Schottky Diode SOD106 MMSZ4690T1G"	"Z1, Z2, Z3, Z4, Z5, Z6, Z7, Z8, Z9, Z10, Z11, Z12, Z13, Z14"	"SOD123"	"ZENER DIODE 5.6V"

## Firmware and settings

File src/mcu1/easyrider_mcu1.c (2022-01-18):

/*
 *
 *  Copyright (C) Bas Brugman
 *  http://www.visionnaire.nl
 *
 *  Licensed under the Apache License, Version 2.0 (the "License");
 *  you may not use this file except in compliance with the License.
 *  You may obtain a copy of the License at
 *
 *    http://www.apache.org/licenses/LICENSE-2.0
 *
 *  Unless required by applicable law or agreed to in writing, software
 *  distributed under the License is distributed on an "AS IS" BASIS,
 *  WITHOUT WARRANTIES OR CONDITIONS OF ANY KIND, either express or implied.
 *  See the License for the specific language governing permissions and
 *  limitations under the License.
 *
 */
#include "easyrider_mcu1.h"

#include <avr/eeprom.h>
#include <avr/interrupt.h>
#include <avr/io.h>
#include <avr/pgmspace.h>
#include <avr/power.h>
#include <avr/sleep.h>
#include <avr/wdt.h>
#include <stdint.h>
#include <stdlib.h>
#include <string.h>

#include "../command.h"
#include "sound.h"

// callbacks struct array: main handler functions and pre-guard functions for
// the queued events
tCallBack g_callbacks[] = {
    {EV_READ_BATTERY, check_battery_read, process_battery},
    {EV_READ_TEMPERATURE, check_temperature_read, process_temperature},
    {EV_READ_CURRENT, check_board_current, process_board_current},
    {EV_READ_ACCEL, check_board_accel, process_board_accel},
    {EV_G1_OFF, check_gear1_off, process_gear1_off},
    {EV_G2_OFF, check_gear2_off, process_gear2_off},
    {EV_G3_OFF, check_gear3_off, process_gear3_off},
    {EV_G4_OFF, check_gear4_off, process_gear4_off},
    {EV_G1_ON, check_gear1_on, process_gear1_on},
    {EV_G2_ON, check_gear2_on, process_gear2_on},
    {EV_G3_ON, check_gear3_on, process_gear3_on},
    {EV_G4_ON, check_gear4_on, process_gear4_on}};

// Gets called from the main loop, generates events and puts them in the event
// queue. The complete queue is handled (emptied) in each main loop iteration in
// a FIFO way, so better put the higher priority events at the top
static void dispatch_events() {
  check_battery();
  check_current();
  check_temperature();
  check_accel();
  check_gear1();
  check_gear2();
  check_gear3();
  check_gear4();
  check_neutral();
  check_sound();
}

// default function for checking sense pins and dispatching events
void check_default(uint8_t event_on, uint8_t event_off, uint8_t pin,
                   volatile uint8_t *debounce_timer_flag,
                   volatile uint8_t *debounce_state) {
  // keep checking for 6 positives in a short timespan, so we're certain a
  // button is pressed/released and it's not noise
  if (*debounce_timer_flag) {  // timer-based flag is set (again)
    *debounce_timer_flag = 0;  // reset to wait for next timer event
    if (pin) {
      *debounce_state =
          (*debounce_state << 1);  // add 0 as a positive "off" press
      if ((*debounce_state & 0b00111111) == 0) {
        set_event(event_off);
      }
    } else {
      *debounce_state =
          (*debounce_state << 1) | 1;  // add 1 as a positive "on" press
      if ((*debounce_state & 0b00111111) == 0b00111111) {
        set_event(event_on);
      }
    }
  }
}

void check_gear1() {
  check_default(EV_G1_ON, EV_G1_OFF, STATUS_C90_SENSE_G1, &FLAG_DEBOUNCE_G1,
                &g_gear1_debounce);
}

void check_gear2() {
  check_default(EV_G2_ON, EV_G2_OFF, STATUS_C90_SENSE_G2, &FLAG_DEBOUNCE_G2,
                &g_gear2_debounce);
}

void check_gear3() {
  check_default(EV_G3_ON, EV_G3_OFF, STATUS_C90_SENSE_G3, &FLAG_DEBOUNCE_G3,
                &g_gear3_debounce);
}

void check_gear4() {
  check_default(EV_G4_ON, EV_G4_OFF, STATUS_C90_SENSE_G4, &FLAG_DEBOUNCE_G4,
                &g_gear4_debounce);
}

void check_neutral() {
  if (g_neutral_counter >= 100) {  // every 0.5s (5ms*100) check
    g_neutral_counter = 0;
    if (g_gear) {
      set_gear(0);  // only set neutral when not in neutral already
    }
  }
}

void check_battery() { set_event(EV_READ_BATTERY); }

void check_current() { set_event(EV_READ_CURRENT); }

void check_temperature() { set_event(EV_READ_TEMPERATURE); }

void check_accel() { set_event(EV_READ_ACCEL); }

uint8_t check_battery_read() { return 1; }

uint8_t check_board_current() { return 1; }

uint8_t check_temperature_read() { return 1; }

uint8_t check_board_accel() { return 1; }

uint8_t check_gear1_on() { return (g_current_gear != 1); }

uint8_t check_gear2_on() { return (g_current_gear != 2); }

uint8_t check_gear3_on() { return (g_current_gear != 3); }

uint8_t check_gear4_on() { return (g_current_gear != 4); }

uint8_t check_gear1_off() { return (g_current_gear == 1); }

uint8_t check_gear2_off() { return (g_current_gear == 2); }

uint8_t check_gear3_off() { return (g_current_gear == 3); }

uint8_t check_gear4_off() { return (g_current_gear == 4); }

// get the next event from the event queue (circular buffer)
uint8_t get_event() {
  uint8_t ev;
  if (g_buffer_tail != g_buffer_head) {  // not empty
    ev = g_event_buffer[g_buffer_tail];
    g_buffer_tail++;
    if (g_buffer_tail >= C90_EVENT_BUFFER_SIZE) {
      g_buffer_tail = 0;
    }
    return ev;
  } else {
    return EV_VOID;  // no events, return a void event
  }
}

// put an event in the event queue (circular buffer)
void set_event(uint8_t ev) {
  g_event_buffer[g_buffer_head] = ev;  // insert event at head position
  g_buffer_head++;                     // advance head
  if (g_buffer_head >= C90_EVENT_BUFFER_SIZE) {
    g_buffer_head = 0;  // cycle back to start
  }
  if (g_buffer_head == g_buffer_tail) {
    g_buffer_tail++;  // also move tail, basically destroying the oldest event
                      // to make space
  }
  if (g_buffer_tail >= C90_EVENT_BUFFER_SIZE) {
    g_buffer_tail = 0;  // cycle back to start
  }
}

// sets the gear
static void set_gear(uint8_t gear) { g_gear = gear; }

// calculates the battery's voltage
// Vref = 5v, if Vref isnt exactly 5.00v, but a bit off, tweak
// C90_OFFSET_ADC_READING for 12v battery readout: my voltage divider
// ratio: 2.2K - 1K Vmeasure:  0.3125 * Vbat 10bit ADCvalue (0-1023):
// Vmeasure/(5/1024) Vbat: (ADCvalue*(5/1024))/(0.3125)
void process_battery() {
  if (FLAG_READ_BATTERY) {
    g_voltage = 49 * g_adc_voltage[3] / 3.125;
    FLAG_READ_BATTERY = 0;
  }
}

// calculates the current consumption of the board in mA, according the sensor's
// voltage output sampled by the ADC default output of the sensor at 0mA
// is 2.5V, 512 ADC, since it can measure AC current and it's hooked up in
// reverse, this value drops when the current increases (using the 0-512 10bit
// part instead of 512-1023) 10bit ADCvalue (0-1023): (5v/1024) -> 0.00488 volt
// per bit resolution sensor: 185mV/A -> 0.0185 volt == 100mA -> 0.00488/0.0185
// == 26mA per bit -> due to low res/noise set to a sensible 25mA/bit
void process_board_current() {
  if (FLAG_READ_CURRENT) {
    g_current = abs(512 - g_adc_voltage[4]) * 25;
    FLAG_READ_CURRENT = 0;
  }
}

// calculates the board's ambient temperature using an LM35 sensor which gives
// 10mV/Celsius since 1 bit is roughly 5mV, max resolution is 0.5 degrees Vref =
// 5v, if Vref isnt exactly 5.00v, but a bit off, tweak C90_OFFSET_ADC_READING
// 10bit ADCvalue (0-1023): Vmeasure/(5/1024) -> use 49*voltage == temperature
// (divide by 100) on receiver side
void process_temperature() {
  if (FLAG_READ_TEMPERATURE) {
    g_temperature = (49 * g_adc_voltage[5]);
    FLAG_READ_TEMPERATURE = 0;
  }
}

// reads the accelerometer's x-/y-/z-axis
// 1.5g setting:  Sensitivity: 800 mV/g  -1g = 850mV  0g = 1650mV 1g = 2450mV
// Vref = 5v, if Vref isnt exactly 5.00v, but a bit off, tweak
// C90_OFFSET_ADC_READING 10bit ADCvalue (0-1023): Vmeasure/(5/1024)
void process_board_accel() {
  if (FLAG_READ_ACCEL) {
    g_accelx = g_adc_voltage[0];
    g_accely = g_adc_voltage[1];
    g_accelz = g_adc_voltage[2];
    FLAG_READ_ACCEL = 0;
  }
}

void process_gear1_on() {
  set_gear(1);
  g_current_gear = 1;
}

void process_gear1_off() {
  g_current_gear = 0;  // assume a neutral until next gear_on changes it again
}

void process_gear2_on() {
  set_gear(2);
  g_current_gear = 2;
}

void process_gear2_off() {
  g_current_gear = 0;  // assume a neutral until next gear_on changes it again
}

void process_gear3_on() {
  set_gear(3);
  g_current_gear = 3;
}

void process_gear3_off() {
  g_current_gear = 0;  // assume a neutral until next gear_on changes it again
}

void process_gear4_on() {
  set_gear(4);
  g_current_gear = 4;
}

void process_gear4_off() {
  g_current_gear = 0;  // assume a neutral until next gear_on changes it again
}

void init_ports() {
  // gear sense pins DDR/PORT: as input(0)/high(1)
  DDR_C90_SENSE_G1 &= ~(1 << PIN_C90_SENSE_G1);
  PORT_C90_SENSE_G1 |= (1 << PIN_C90_SENSE_G1);
  DDR_C90_SENSE_G2 &= ~(1 << PIN_C90_SENSE_G2);
  PORT_C90_SENSE_G2 |= (1 << PIN_C90_SENSE_G2);
  DDR_C90_SENSE_G3 &= ~(1 << PIN_C90_SENSE_G3);
  PORT_C90_SENSE_G3 |= (1 << PIN_C90_SENSE_G3);
  DDR_C90_SENSE_G4 &= ~(1 << PIN_C90_SENSE_G4);
  PORT_C90_SENSE_G4 |= (1 << PIN_C90_SENSE_G4);
  // RPM T0 counter pin as as input(0)/high(1)
  DDR_C90_RPM &= ~(1 << PIN_C90_RPM);
  PORT_C90_RPM |= (1 << PIN_C90_RPM);
  // heartbeat led on pcb
  DDR_C90_HEARTBEAT_LED |= (1 << PIN_C90_HEARTBEAT_LED);
  PORT_C90_HEARTBEAT_LED |= (1 << PIN_C90_HEARTBEAT_LED);
  // buzzer
  DDR_C90_BUZZER |= (1 << PIN_C90_BUZZER);    // output
  PORT_C90_BUZZER &= ~(1 << PIN_C90_BUZZER);  // low
}

// setup the ADC in Free Running Mode (3 LSB in ADCSRB: 0 by default), so we can
// advance the read pin ourselves
void enable_adc() {
  // analog input channel selections,  clear the bottom 3 bits before setting
  // the new pin for readout the 3 LSB select the currently active  ADC0-7
  ADMUX = (ADMUX & 0xF8) | g_adc_read_pin;
  ADMUX |= (1 << REFS0);  // voltage reference = AVCC
  DIDR0 = 0x3F;           // 0b00111111, disable digital inputs for ADC0-ADC5
  ADCSRA |= (1 << ADEN);  // enable ADC
  ADCSRA |= (1 << ADPS2) | (1 << ADPS1) | (1 << ADPS0);  // prescaler = 128
  ADCSRA |= (1 << ADIE);                                 // enable interrupt
  ADCSRA |= (1 << ADSC);                                 // start a conversion
}

ISR(ADC_vect) {
  // first read ADCL, then ADCH to keep it an atomic operation
  g_adc_voltage[g_adc_read_pin] = ADCL;
  g_adc_voltage[g_adc_read_pin] =
      (g_adc_voltage[g_adc_read_pin] | (ADCH << 8));  // ADCH has the last 2
                                                      // bits as LSB, which
                                                      // become MSB in uint16_t
  g_adc_voltage[g_adc_read_pin] += C90_OFFSET_ADC_READING;
  g_adc_read_pin++;  // increment pin to read a new voltage on
  if (g_adc_read_pin > 5) {
    g_adc_read_pin = 0;
  }
  ADMUX = (ADMUX & 0xF8) | g_adc_read_pin;
  ADCSRA |= (1 << ADSC);  // start another conversion again
}

// RPM timer
void start_rpm_timer() {
  // Configure timer 0 (8-bit) for CTC mode (Clear on Timer Compare)
  // set timer as CTC Mode
  TCCR0A |= (1 << WGM01);
  TCCR0A |= ~(1 << WGM00);
  TCCR0A &= ~((1 << COM0A1) |
              (1 << COM0A0));  // DON'T use PB3's OC0A functionality, else it
                               // will interfere with the buzzer on that pin
  TCCR0B |= ~(1 << WGM02);
  // no prescale, but configure as external clock source on T0 pin. Clock on
  // falling edge.
  TCCR0B |= ((1 << CS01) | (1 << CS02));
  TCCR0B &= ~(1 << CS00);
  TIMSK0 |= (1 << OCIE0A);  // Enable Compare A interrupt
  OCR0A = 1;  // Set CTC compare A value to 1, to calculate the time between
              // each pulse
}

void start_buzzer_timer() {
  // Configure timer 1 (16-bit) for CTC mode (Clear on Timer Compare)
  TCCR1A &= ~((1 << WGM11) | (1 << WGM10));  // CTC Mode
  TCCR1B |= (1 << WGM12);                    // CTC Mode
  TCCR1B |= ((1 << CS11) | (1 << CS10));     // prescale 64
  TCCR1B &= ~(1 << CS12);                    // prescale 64
  // Set CTC compare value, approx. 4600hz: with a square wave that is a 2300hz
  // tone This is the default value, when playing sounds, this value is
  // constantly updated with the tone's frequency
  OCR1A = 68;
}

// sense timer for debouncing the gear senses
void start_sense_timer() {
  // Configure timer 2 (8-bit) for CTC mode (Clear on Timer Compare)
  // set timer as CTC Mode
  TCCR2A |= (1 << WGM21);
  TCCR2A |= ~(1 << WGM20);
  TCCR2B |= ~(1 << WGM22);
  // prescale 1024
  TCCR2B |= ((1 << CS20) | (1 << CS21) | (1 << CS22));
  TIMSK2 |= (1 << OCIE2A);  // Enable Compare A interrupt
  OCR2A = 97;  // Set CTC compare A value, approx. 5 ms -> 200 times/sec
}

// timer for the period calculation of the RPM
void start_10us_timer() {
  // Configure timer 3 (16-bit) for CTC mode (Clear on Timer Compare)
  TCCR3A &= ~((1 << WGM31) | (1 << WGM30));  // CTC Mode
  TCCR3B |= (1 << WGM32);                    // CTC Mode
  // prescale with 8 to get 2.5million hz with a 20mhz crystal
  TCCR3B &= ~((1 << CS30) | (1 << CS32));
  TCCR3B |= (1 << CS31);
  TIMSK3 |= (1 << OCIE3A);  // Enable Compare A interrupt
  OCR3A = 24;               // Set CTC compare value, 100.000 times/sec
}

// interrupt handler for 8bit timer0 that triggers every RPM pulse
// resolution of RPM is 120RPM per bit steps
ISR(TIMER0_COMPA_vect) {
  // calculate RPM by checking how many 10 microsecond ticks have passed since
  // last pulse, the multiply by 2 is needed since we only detect the positive
  // pulse of the rectified signal
  g_rpm = (100000UL / g_10us_ticks * 60) * 2;
  // reset ticks
  g_10us_ticks = 0;
  // reset to full to notify that we still have rpms
  g_rpm_reset = 40;
}

// timer interrupt for the speaker
ISR(TIMER1_COMPA_vect) {
  // toggle buzzer pin to create a 50% duty cycle
  PORT_C90_BUZZER ^= (1 << PIN_C90_BUZZER);
}

// timer interrupt for the sense, each 5ms
ISR(TIMER2_COMPA_vect) {
  // reset rpm to 0 when engine stalls
  if (g_rpm_reset > 0) {
    g_rpm_reset--;
  } else if (g_rpm) {
    g_rpm = 0;
  }
  // neutral check after g_current_gear == 0 for # counts
  if (!g_current_gear) {
    g_neutral_counter++;
  } else {
    g_neutral_counter = 0;
  }
#ifdef EASY_TRACE123
  g_uart_display_counter++;
#endif
  FLAG_READ_BATTERY = 1;
  FLAG_READ_CURRENT = 1;
  FLAG_READ_TEMPERATURE = 1;
  FLAG_READ_ACCEL = 1;
  FLAG_DEBOUNCE_G1 = 1;
  FLAG_DEBOUNCE_G2 = 1;
  FLAG_DEBOUNCE_G3 = 1;
  FLAG_DEBOUNCE_G4 = 1;
  if (g_music_duration) {
    g_music_duration--;
  }
}

// timer interrupt with 10 microsecond intervals to calculate RPM
ISR(TIMER3_COMPA_vect) { g_10us_ticks++; }

void check_sound() {
  if (FLAG_MUSIC) {
    if (!g_music_duration) {
      if (pgm_read_word(g_current_music)) {  // get note data until MUSIC_END
        if (g_current_music ==
            g_selected_music) {  // still at start: first byte is the tempo
          g_music_tempo = pgm_read_word(g_current_music);
          g_current_music++;
        }
        g_music_duration =
            calc_note_duration(pgm_read_word(g_current_music), g_music_tempo);
        g_current_music++;
        if (pgm_read_word(g_current_music) ==
            MUSIC_P) {               // pause check (silence for a certain time)
          TIMSK1 &= ~(1 << OCIE1A);  // disable interrupt
          PORT_C90_BUZZER &= ~(1 << PIN_C90_BUZZER);
        } else {
          TIMSK1 |= (1 << OCIE1A);  // enable interrupt
        }
        OCR1A = pgm_read_word(g_current_music);
        TCNT1 = 0;
        g_current_music++;
      } else {  // the end of song
        FLAG_MUSIC = 0;
        TIMSK1 &= ~(1 << OCIE1A);  // disable interrupt
        PORT_C90_BUZZER &= ~(1 << PIN_C90_BUZZER);
      }
    }
  }
}

void set_sound(uint8_t status) {
  uint8_t song_idx;
  // initially mute current sound
  TIMSK1 &= ~(1 << OCIE1A);  // disable interrupt
  PORT_C90_BUZZER &= ~(1 << PIN_C90_BUZZER);
  FLAG_MUSIC = 0;
  switch (status) {
    case 255:  // random song
      srand(g_adc_voltage[0] + g_adc_voltage[1] + g_adc_voltage[2] +
            g_adc_voltage[3]);               // random seed
      song_idx = 1 + (uint8_t)(rand() % 5);  // add 0-4 idx
      g_music_duration = 0;
      g_current_music = (uint16_t *)pgm_read_word(&g_music[song_idx]);
      g_selected_music = (uint16_t *)pgm_read_word(&g_music[song_idx]);
      FLAG_MUSIC = 1;
      break;
    case 254:  // no sound, do nothing
      break;
    case 253:  // beep only
      OCR1A = 68;
      TCNT1 = 0;
      TIMSK1 |= (1 << OCIE1A);  // enable interrupt
      break;
    default:  // specific idx
      g_music_duration = 0;
      g_current_music = (uint16_t *)pgm_read_word(&g_music[status]);
      g_selected_music = (uint16_t *)pgm_read_word(&g_music[status]);
      FLAG_MUSIC = 1;
  }
}

void initialize() {
  MCUCR = 0x80;  // disable JTAG at runtime (2 calls in a row needed)
  MCUCR = 0x80;
  wdt_enable(WDTO_2S);                // enable 2 sec watchdog
  sei();                              // enable global interrupts
  g_buffer_head = g_buffer_tail = 0;  // init event buffer
  enable_adc();
  init_ports();
  start_rpm_timer();
  start_buzzer_timer();
  start_sense_timer();
  start_10us_timer();
  command_init();
}

int main(void) {
  initialize();
  while (1) {
    dispatch_events();
    while ((g_event = get_event()) !=
           EV_VOID) {  // handle the complete event queue in one go
      for (uint8_t i = 0; i < TR_CNT; i++) {
        if (g_event == g_callbacks[i].event) {  // check if event matches
          if (g_callbacks[i].check_func()) {    // guard condition to check if
                                              // current state is accepting this
                                              // event
            g_callbacks[i].process_func();  // call event handler
            break;
          }
        }
      }
    }
    //  WiFi serial wifly passthrough of UART1 cable -> UART0 Wifi (mcu1)
    //  or
    //  GPS passthrough of UART1 cable -> UART0 GPS (mcu2)
    /*if (uart_available_1()) {*/
    /*uart_put_0(uart_get_1());*/
    /*}*/
    /*if (uart_available_0()) {*/
    /*uart_put_1(uart_get_0());*/
    /*}*/
    // process all commands (SPI, UART and WIFI)
    command_process();
#ifdef EASY_TRACE123
    if (g_uart_display_counter >= 20) {
      g_uart_display_counter = 0;
      uart_put_str_1("accelx: ");
      uart_put_int_1(g_accelx);
      uart_put_str_1("\r\n");
      uart_put_str_1("accely: ");
      uart_put_int_1(g_accely);
      uart_put_str_1("\r\n");
      uart_put_str_1("accelz: ");
      uart_put_int_1(g_accelz);
      uart_put_str_1("\r\n");
      uart_put_str_1("voltage: ");
      uart_put_int_1(g_voltage);
      uart_put_str_1("\r\n");
      uart_put_str_1("current: ");
      uart_put_int_1(g_current);
      uart_put_str_1("\r\n");
      uart_put_str_1("temperature: ");
      uart_put_int_1(g_temperature);
      uart_put_str_1("\r\n");
      uart_put_str_1("rpm: ");
      uart_put_int_1(g_rpm);
      uart_put_str_1("\r\n");
      uart_put_str_1("gear: ");
      uart_put_int_1(g_gear);
      uart_put_str_1("\r\n");
    }
#endif
    if (!g_mcu_reset) {
      wdt_reset();  // reset the watchdog, i.e. don't reset the mcu
    }
  }
  return 0;  // keep C-compiler happy, although will never reach this point
}

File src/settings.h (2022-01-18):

/*
 *
 *  Copyright (C) 2014 Bas Brugman
 *  http://www.visionnaire.nl
 *
 */
#ifndef SETTINGS_H_INCLUDED
#define SETTINGS_H_INCLUDED

#include <avr/eeprom.h>
#include <avr/io.h>
#include <stdint.h>
#include <stdlib.h>
#include <string.h>

#define ROM_SYSTEM_NAME "easyrider"
#define ROM_POWER_CYCLES 0
#define ROM_PINCODE "0000"
#define ROM_SD_LOG 0
#define ROM_SW_VERSION 100
#define ROM_HW_VERSION "rev B"
#define ROM_P_SENSES_ACTIVE 65535
#define ROM_D_SENSES_ACTIVE 0
#define ROM_ALARM_SETTLE_TIME 800
#define ROM_INDICATOR_SOUND 1
#define ROM_BLINK_SPEED 9765
#define ROM_ALARM_COUNTER 6
#define ROM_ALARM_TRIGGER 18
#define ROM_ALARM_TRIGGER_COUNTER 4
#define ROM_ALARM_THRES_MIN 140
#define ROM_ALARM_TRHES_MAX 550
#define ROM_STARTUP_SOUND 255

// settings saved in EEPROM
typedef struct {
  char system_name[10];   // contains the string: "easyrider", not changeable,
                          // used to check for correctly filled in EEPROM
                          // settings
  uint16_t power_cycles;  // number of startups of mcu, default: 0
  char pincode[5];  // // authentication for app over Wifi, default: "0000"
  uint8_t sd_log;   // flag to log to microSD card, default: 0
  uint16_t
      sw_version;  // firmware version (software), e.g. 435 -> version 4.3.5
  char hw_version[10];         // board version (hardware), e.g. "rev b"
  uint16_t p_senses_active;    // default: 65535 (0xFFFF), all active
  uint16_t d_senses_active;    // default: 0 (0x0000), all inactive
  uint16_t alarm_settle_time;  // default 800: 5ms ticks, so 4 secs
  uint8_t indicator_sound;     // default 1: beep when indicators blink
  uint16_t
      blink_speed;  // default 9765: 1 tick is 0.0000512 secs -> 0.5secs on/off
  uint8_t alarm_counter;  // default 6 times: 3 times on and 3 times off
  uint8_t alarm_trigger;  // default 18: voltage offset 18 * 5V/1024 parts
  uint8_t alarm_trigger_counter;  // default 4: we need 4 times a postive alarm
                                  // trigger, each measurement is done TIMER1
                                  // (0.5s) tick
  uint16_t alarm_thres_min;       // default 140: voltage minimum 0.685
  uint16_t alarm_thres_max;       // default 550: voltage maximum 2.685
  uint8_t startup_sound;  // default 255: random, [0-252] index of music array,
                          // no sound: 254, beep only: 253
} tSettings;

void read_settings(tSettings *settings);
void update_settings(tSettings *settings);
void reset_settings(void);

#endif

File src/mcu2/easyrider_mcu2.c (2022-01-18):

/*
 *
 *  Copyright (C) Bas Brugman
 *  http://www.visionnaire.nl
 *
 */
#include <avr/eeprom.h>
#include <avr/interrupt.h>
#include <avr/io.h>
#include <avr/pgmspace.h>
#include <avr/power.h>
#include <avr/sleep.h>
#include <avr/wdt.h>
#include <stdint.h>
#include <stdlib.h>
#include <string.h>
#include <util/delay.h>

#include "easyrider_mcu2.h"

// state transition struct array: main handler functions and pre-guard functions
// for the queued events
tTransition g_trans[] = {
    {EV_BRAKE_ON, check_brake_on, process_brake_on},
    {EV_BRAKE_OFF, check_brake_off, process_brake_off},
    {EV_CLAXON_ON, check_claxon_on, process_claxon_on},
    {EV_CLAXON_OFF, check_claxon_off, process_claxon_off},
    {EV_RI_ON, check_ri_on, process_ri_on},
    {EV_RI_OFF, check_ri_off, process_ri_off},
    {EV_LI_ON, check_li_on, process_li_on},
    {EV_LI_OFF, check_li_off, process_li_off},
    {EV_WARNING_ON, check_warning_on, process_warning_on},
    {EV_WARNING_OFF, check_warning_off, process_warning_off},
    {EV_IGN_ON, check_ign_on, process_ign_on},
    {EV_IGN_OFF, check_ign_off, process_ign_off},
    {EV_PILOT_ON, check_pilot_on, process_pilot_on},
    {EV_PILOT_OFF, check_pilot_off, process_pilot_off},
    {EV_LIGHT_ON, check_light_on, process_light_on},
    {EV_LIGHT_OFF, check_light_off, process_light_off},
    {EV_NEUTRAL_ON, check_neutral_on, process_neutral_on},
    {EV_NEUTRAL_OFF, check_neutral_off, process_neutral_off},
    {EV_ALARM_ON, check_alarm_on, process_alarm_on},
    {EV_ALARM_OFF, check_alarm_off, process_alarm_off}};

static void set_state(uint16_t st) {
  g_state = st;
  command_trigger_state(CMD_IF_IC);
#ifdef EASY_TRACE
  command_trigger_state(CMD_IF_DEBUG);
#endif
}

static uint16_t get_substate(uint16_t st) { return (g_state & st); }

static void set_substate(uint16_t st) {
  g_state |= st;
  command_trigger_state(CMD_IF_IC);
#ifdef EASY_TRACE
  command_trigger_state(CMD_IF_DEBUG);
#endif
}

static void remove_substate(uint16_t st) {
  g_state &= ~st;
  command_trigger_state(CMD_IF_IC);
#ifdef EASY_TRACE
  command_trigger_state(CMD_IF_DEBUG);
#endif
}

// Gets called from the main loop, reads all senses and puts them in the event
// queue. The complete queue is handled (emptied) in each main loop iteration in
// a FIFO way, so better put the higher priority events at the top, i.e. claxon
// sound is more important then indicator light.
static void dispatch_events() {
  check_brake();   // high prio, critical
  check_claxon();  // high prio, critical
  check_light();
  check_ri();
  check_li();
  check_warning();
  check_pilot();
  check_alarm();
  check_alarm_settle();
  check_alarm_trigger();
  check_neutral();
  check_rtc();
  check_stats();
  check_gps();
  check_ign();
}

uint8_t check_brake_on() {
  return ((g_state & ~(ST_BRAKE | ST_ALARM | ST_SLEEP)) == g_state);
}

uint8_t check_brake_off() { return (g_state & ST_BRAKE); }

uint8_t check_claxon_on() {
  return ((g_state & ~(ST_CLAXON | ST_ALARM | ST_SLEEP)) == g_state);
}

uint8_t check_claxon_off() { return (g_state & ST_CLAXON); }

uint8_t check_pilot_on() {
  return ((g_state & ~(ST_PILOT | ST_ALARM | ST_SLEEP)) == g_state);
}

uint8_t check_pilot_off() { return (g_state & ST_PILOT); }

uint8_t check_light_on() {
  return ((g_state & ~(ST_LIGHT | ST_ALARM | ST_SLEEP)) == g_state);
}

uint8_t check_light_off() { return (g_state & ST_LIGHT); }

uint8_t check_neutral_on() {
  return ((g_state & ~(ST_NEUTRAL | ST_ALARM | ST_SLEEP)) == g_state);
}

uint8_t check_neutral_off() { return (g_state & ST_NEUTRAL); }

uint8_t check_ign_on() {
  return ((g_state & (ST_SLEEP | ST_ALARM)) == g_state);
}

uint8_t check_ign_off() {
  return ((g_state & ~(ST_SLEEP | ST_ALARM)) == g_state);
}

uint8_t check_ri_on() {
  return ((g_state & ~(ST_WARNING | ST_LI | ST_ALARM | ST_SLEEP)) == g_state);
}

uint8_t check_ri_off() { return (g_state & ST_RI); }

uint8_t check_li_on() {
  if (SPCR & (1 << SPE))
    return 0;  // extra check to ignore SI_LI when SPI transfer is active, since
               // this SS pin is an output(1) during SPI hardware mode
  return ((g_state & ~(ST_WARNING | ST_RI | ST_ALARM | ST_SLEEP)) == g_state);
}

uint8_t check_li_off() {
  if (SPCR & (1 << SPE))
    return 0;  // extra check to ignore SI_LI when SPI transfer is active, since
               // this SS pin is an output(1) during SPI hardware mode
  return (g_state & ST_LI);
}

// warning blinks override RI/LI
uint8_t check_warning_on() {
  return ((g_state & ~(ST_ALARM | ST_SLEEP)) == g_state);
}

uint8_t check_warning_off() { return (g_state & ST_WARNING); }

uint8_t check_alarm_on() {
  return ((g_state & ST_ACTIVE) && ((g_state & ~ST_ALARM_SET) == g_state));
}

uint8_t check_alarm_off() {
  return ((g_state & ST_ALARM_SET) &&
          ((g_state & ~(ST_ALARM | ST_SLEEP)) == g_state));
}

// default function for checking sense pins and dispatching events
void check_default(uint16_t sense_flag, uint8_t event_on, uint8_t event_off,
                   uint8_t pin, volatile uint8_t *debounce_timer_flag,
                   volatile uint8_t *debounce_state) {
  // physical senses
  if ((g_settings.p_senses_active & sense_flag) == sense_flag) {
    // keep checking for 6 positives in a short timespan, so we're certain a
    // button is pressed/released and it's not noise timespan is 6*5ms, so the
    // delay is 30ms
    if (*debounce_timer_flag) {  // timer-based flag is set (again)
      *debounce_timer_flag = 0;  // reset to wait for next timer event
      if (pin) {
        *debounce_state =
            (*debounce_state << 1);  // add 0 as a positive "off" press
        if ((*debounce_state & 0b00111111) == 0) {
          set_event(event_off);
        }
      } else {
        *debounce_state =
            (*debounce_state << 1) | 1;  // add 1 as a positive "on" press
        if ((*debounce_state & 0b00111111) == 0b00111111) {
          set_event(event_on);
        }
      }
    }
  }
  // dynamic senses
  if ((g_settings.d_senses_active & sense_flag) == sense_flag) {
    if ((g_d_senses_status & sense_flag) == sense_flag) {
      set_event(event_on);
    } else {
      set_event(event_off);
    }
  }
}

void check_brake() {
  check_default(FLAG_SENSE_BRAKE, EV_BRAKE_ON, EV_BRAKE_OFF,
                STATUS_C90_SENSE_BRAKE, &FLAG_DEBOUNCE_BRAKE,
                &g_brake_debounce);
}

void check_claxon() {
  check_default(FLAG_SENSE_CLAXON, EV_CLAXON_ON, EV_CLAXON_OFF,
                STATUS_C90_SENSE_CLAXON, &FLAG_DEBOUNCE_CLAXON,
                &g_claxon_debounce);
}

void check_pilot() {
  check_default(FLAG_SENSE_PILOT, EV_PILOT_ON, EV_PILOT_OFF,
                STATUS_C90_SENSE_PILOT, &FLAG_DEBOUNCE_PILOT,
                &g_pilot_debounce);
}

void check_light() {
  check_default(FLAG_SENSE_LIGHT, EV_LIGHT_ON, EV_LIGHT_OFF,
                STATUS_C90_SENSE_LIGHT, &FLAG_DEBOUNCE_LIGHT,
                &g_light_debounce);
}
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
